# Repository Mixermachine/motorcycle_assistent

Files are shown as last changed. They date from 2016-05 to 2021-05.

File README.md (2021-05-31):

# Motorcycle Assistent

## Describtion
I created this project to equipe my BMW F650 GS motorcycle with a little assitent including a digital chain oiler.<br />

What is a chain oiler? <br />
A chain oiler drops a little amount of oil on the heavily stressed motorcycle chain.<br />
This way the chain lasts longer. <br />

Why a digital chain oiler? <br />
Regular chain oilers are often not precise, hard to adjust and finaly quite expensive.<br />
In this project I use verily cheap components with an easy-to-use interface.<br />

For controlling my Assistent I added a display, external chips and one button.<br />
The program variables, log and comments are all written in english.<br />
The user interface is designed for German users.<br />
I could provide a interface for Englisch users if there is a need for it.<br />

It runs on the Arduino/Genuino Nano and Arduino/Genuino Uno<br />

## Features:
+ Trigger the chain oiler pump after a given periode of time for a little interval
+ Display temperature
+ Display battery voltage
+ Display date and time (dim display accourding to the time)
+ Provide a menu for the settings
+ Power saving mode
+ Crank assistent (shows lowest voltage and the duration)

## Hardware:
+ Arduino nano/uno   (Uno for development, Nano for the actual use in my motorcycle)
+ SSD1306 display
+ DS18B20 temperature sensor
+ DS3231 clock chip
+ 2 * 4,7k, 2 * 12k Ohm Resistor
+ Button
+ Energy-saving voltage regulator (not compulsory, MCP1703 recomended)
+ Wiring

## Libraries
+ SPI.h (screen)
+ Wire.h (screen and clock)
+ Adafruit_GFX.h (screen)
+ Adafruit_SSD1306.h (screen)
+ OneWire.h (temperature)
+ DS3231.h (clock)
+ EEPROM.h (EEPROM memory)
+ LowPower.h (power saving)

## Chain oiler
The chain oiler can be trimmed to your needs.<br />
The pump duration time, the interval time and the state (if it works at all) can be easily set in the menu.<br />
All settings are saved in the internal memory (EEPROM) and will be loaded with each power up.<br />
The chain oiler only works if the battery voltage is above 13,2V.<br />
This is no technical limitation, but a safety one.<br />
On my F650 I needed to grab power from the rear lights, which means if I leave the parking lights on my bike on, the Arduino is still powered.<br />
If the engine is running, the generator will hold the voltage at 13,5V to 14,2V -> which means the chain oiler will run if it is set active.<br />

## Typical display faces
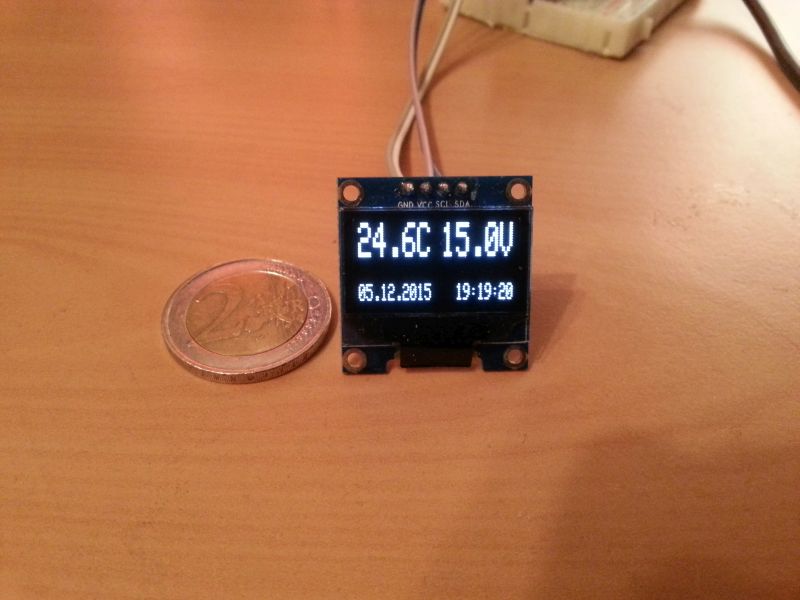
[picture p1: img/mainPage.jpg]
Main page


After a long click on the button (1 second, state 2016-05-12) the menu will open

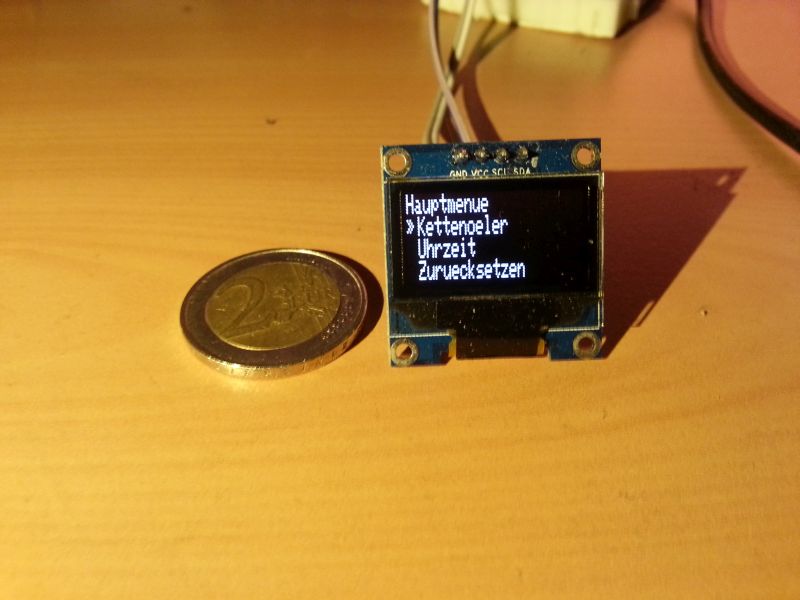
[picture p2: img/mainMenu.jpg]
Main menu


With a short click on the button you move the cursor one step further down (on the last entry it will jump back up again).<br />
With a long click on the button you enter submenus and select options.<br />
As long you are in the menu the chain oiler and all other components will remain in standby.<br />

## Voltage regulator and power saving
I recommend to replace the onboard voltage regulator with one which has less quiescent current (current which the regulator needs for itself) if you are planning to use the power saving mode. <br />
The standard one uses about 10 mA and requiers at least 7V to produce a good 5V line for the Arduino. <br />
The MCP1703 for example uses only 0.003 mA for itself and requiers 0,1V to 0,6V extra above the 5V for the Arduino to work properly. <br />
DC-DC converters do not really make sense here.<br />
Although the converter would be more efficient in the normal work mode, it would be horrible in power saving mode (because it also has a fairly high quiescent current). We don't really need a high efficiency if the engine is running (about 50mA in normal mode). <br />
To decrease the comsumption even more, you can disconnect the power LED of the Arduino.<br />

So if you use the MCP1703 and remove the power LED from the Arduino it will be much more efficient.<br />
The current should be under 0,01 mA. (Needs testing)<br />
The power saving mode will kick in if the voltage is under 12V for longer then 20 seconds.<br />
It will turn of the power of the display, clock and temperature sensor.<br />
Every 2 seconds the Arduino will wake up for under 1 millisecond to check the voltage.<br />
If the voltage is equal or above 12V the Arduino will wake up and return to the normal work mode.<br />

## Schematic

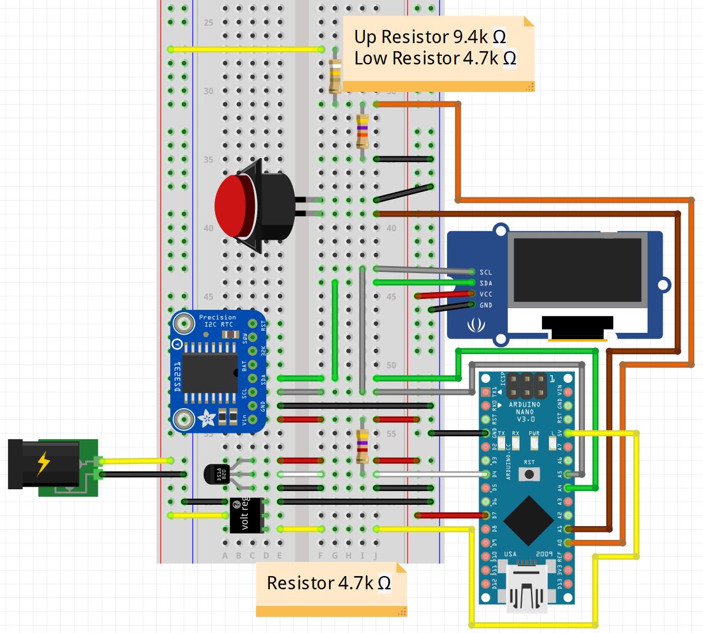
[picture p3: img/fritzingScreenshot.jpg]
Fritzing Schematic
 <br />

## Developer stuff
This project does focus on the highest efficiency possible.<br />
The Atmel328 chip (Arduino Uno, Mini,...) provides 32kb of flash memory and 2 kb of ram.<br />
I could not always focus on best practice code, but tried to keep the work well sorted and well commented.<br />
Flash memory and RAM efficiency was the main goal.<br />
The code offers the possibility of logging via the serial connection of the Arduino.<br />
Change GBL_LOGLEVEL to a value which you like. (0 verbous, 1 info, 2 warning, 3 error).<br />
This project nearly uses the hole flash memory.<br />
(state 2016-05-13, 27 148 Byte of the flash memory is used).<br />

Please open a issue here before you use this Arduino project for a commercial product.

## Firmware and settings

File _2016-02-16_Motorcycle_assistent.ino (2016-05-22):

//**** INCLUDES
//* include for Screen
#include <SPI.h>
#include <Wire.h>
#include <Adafruit_GFX.h>
#include <Adafruit_SSD1306.h>
//*

//* include for DS18B20 temperature sensor
#include <OneWire.h>
//

//* include for DS3231 clock chip
#include <DS3231.h>
//*

// include for EEPROM memory
#include <EEPROM.h>
//*

// include for the power saving sleep library
#include <LowPower.h>
//*

//**** DEFINES
//* define power pin to switch the external chips
#define POWER_PIN_EXTERNAL 7 
//*

//* define for Screen
//#define OLED_RESET 4 // not used here/ nicht genutzt bei diesem Display
Adafruit_SSD1306 display(0); // the value is not important
//#define DRAW_DELAY 118
//#define D_NUM 47
//*

//* define for DS18B20 temperature sensor
#define DS18B20_PIN 4 // PIN for temp sensor
//*

//* define for the voltageDeviderPins and resistorValue
#define VOLTAGE_PIN A0
#define VOLTAGE_RESISTOR1 9400
#define VOLTAGE_RESISTOR2 4700
#define VOLTAGE_POWERDOWN 12
//*

//* define for the buttonPins
#define BUTTON_1 A1
#define BUTTON_2 A2

#define BUTTON_TRIGGER_VALUE 600 // if analogRead returns a value above this value, the button will be triggered
//*

//* define for the CHAIN_OILER_PIN
#define CHAIN_OILER_PIN 6
// standard values for chain_oiler
#define STD_CHAIN_OILER_ACTIVE true
#define STD_CHAIN_OILER_WAIT 600000
#define STD_CHAIN_OILER_PUMP 100
#define STD_CHAIN_OILER_VOLTAGE 13.2
//*

//* define for the logs
#define GBL_LOGLEVEL 1   // set log level here
#define VERBOUS_LOG 0
#define INFO_LOG 1
#define WARNING_LOG 2
#define ERROR_LOG 3
//*

//* defines for the memory management
#define RECORD_PRESENT_ADDR 0  // 1 byte for a byte
#define RECORD_PRESENT_VALUE_0 10 // this works as a versioning control for compactibably 
#define RECORD_PRESENT_VALUE_1 10 // Later versions might changed this number

#define RECORD_CHAIN_OILER_ADDR 2     // 7 bytes to save
//*

//**** GLOBAL VARIABLES
//* power state variables
bool currentExternalPower = false;
unsigned long timeFirstLowVoltage = 0;
uint16_t timeCranking = 0;  // about 65 seconds should be enough time ;)
float lowestCrankVoltage = 0;
float measuredVoltage = 0;
uint16_t timeToWaitPowerDown = 20000; // in milliseconds

//* timing variables
// Main display refresh
unsigned long timeSinceMainDisplayRefresh = 0;  //
#define INTERVAL_MAIN_DISPLAY_REFRESH 1000 // to keep it together, define is placed here. Using define to save ram

// Main button check
// The check is triggered every 100 ms and counts up a value if the button is pressed
// At for example 10 counts a action is triggered. So you need to hold the button down for 1 
unsigned long timeSinceMainButtonCheck = 0;
#define INTERVAL_MAIN_BUTTON_CHECK 100
byte mainButtonCounter = 0;
#define MAIN_BUTTON_COUNTER_TRIGGER 10

//* DS18B20 temperatur sensor
OneWire DS18B20ds(DS18B20_PIN);
byte DS18B20addr[8];

//* DS3231 clock chip
// define the PINS for the clock.
DS3231 DS3231rtc(A4,A5); // first SDA_PIN, second SCL_PIN on DS3231

//* chain oiler timings
boolean chain_oiler_active = STD_CHAIN_OILER_ACTIVE;
unsigned long chain_oiler_wait = STD_CHAIN_OILER_WAIT;  // unsigned long else overflow. standard 10 minutes (600000 ms)
unsigned int chain_oiler_pump = STD_CHAIN_OILER_PUMP;  // how long the pump should run in one intervall
double chain_oiler_voltage = STD_CHAIN_OILER_VOLTAGE; // needs to be tested. Determines if the engine is running
unsigned long timeSinceChainOiler = 0;

//**** setup code
void setup()   {

  //* initialize Serial connection
  Serial.begin(250000);
  //*

  powerManager(true);

  timeSinceChainOiler = millis(); // skip the first run of the chain oiler.
                                  // Nobody wants to spill oil in the garage

  readSettings();  // read settings if saved previously
}

//**** loop code
void loop() {

// meassuring voltage and checking for low voltage power down or cranking

  measuredVoltage = readVoltage();
  if(measuredVoltage <= VOLTAGE_POWERDOWN) {
    // detected low voltage. Can be low battery or cranking
    unsigned long timeFirstCrank = millis();

    if (INFO_LOG >= GBL_LOGLEVEL) {
          Serial.println(F("I: Low voltage detected"));
    }
    // think of the cranking first
    // Crank assistent
    lowestCrankVoltage = measuredVoltage;
    while (measuredVoltage < VOLTAGE_POWERDOWN && (millis() - timeFirstCrank) < timeToWaitPowerDown) {
      if (measuredVoltage < lowestCrankVoltage){ // loop till voltage is higher or voltage is low for a longer time
          lowestCrankVoltage = measuredVoltage;

          // notify user of a new lowest value
          // this takes about 30 ms
          display.clearDisplay();
          display.setTextColor(WHITE);
          display.setTextSize(2);
          display.setCursor(0,0);
          display.println(F("Starten"));
          
          display.setTextSize(1);
          display.println(F("Niedrigste Spannung"));
          
          display.print(measuredVoltage,1);
          display.print('V');
          display.display();

        }
        measuredVoltage = readVoltage();
    }
    
    
    // if the low voltage is still present, go to sleep
    if ((millis() - timeFirstCrank) >= timeToWaitPowerDown) {
      if (WARNING_LOG >= GBL_LOGLEVEL) {
          Serial.println(F("I: Low voltage continues"));
          Serial.println(F("I: Entering power saving mode"));
          Serial.flush(); // wait for the serial data to be transmited before sleeping
      }
      
      // Power saving mode
      powerManager(false);

      while(readVoltage() < VOLTAGE_POWERDOWN) {

        // Power saving mode
        // wake up each two second to check the voltage.
        // sleep time could be lower but to remain a little responsive,
        // two seconds will do
        LowPower.powerDown(SLEEP_2S, ADC_OFF, BOD_OFF);
      }
      
      if (INFO_LOG >= GBL_LOGLEVEL) {
          Serial.println(F("I: Voltage is good again"));
      }
      powerManager(true);      
      
    } else {
      // if it was a simple crank, wait one second to give the user some time
      // to view the displayed value
      if (INFO_LOG >= GBL_LOGLEVEL) {
          Serial.println(F("I: Low voltage was cranking"));
          Serial.print(F("I: Crank lowest voltage="));
          Serial.println(lowestCrankVoltage,1);
          Serial.print(F("I: Crank durration="));
          Serial.println(millis() - timeFirstCrank);
          Serial.flush();  
          // we need to wait for the Serial data to be transfered
          // else the log will be distorted
      }
      
      LowPower.powerDown(SLEEP_1S,ADC_OFF,BOD_OFF);

      // display the time the cranking toke
      display.clearDisplay();
      display.setTextColor(WHITE);
      display.setTextSize(2);
      display.setCursor(0,0);
      display.println(F("Starten"));
      display.setTextSize(1);
      display.println(F("Dauer"));
      // the actual time isn't that accurate.
      // the crank duration can differ.
      // If the Arduino calcs the menu for example then the low voltage detection will be delayed
      // Still it's usefull
      display.print(millis() - timeFirstCrank -8); // it takes 8 ms from the end of the cranking loop till this is calced
      display.print(F("ms"));
      display.display();
      
      LowPower.powerDown(SLEEP_1S,ADC_OFF,BOD_OFF);
    }
  }

  // chain oiler routine
  if(timeSinceChainOiler + chain_oiler_wait <= millis()) {
    timeSinceChainOiler = millis();
    if ( chain_oiler_active) {
      if (readVoltage() >= chain_oiler_voltage) {
        triggerChainOiler(chain_oiler_pump);
      } else {
        if (INFO_LOG >= GBL_LOGLEVEL) {
          Serial.print(F("I: Chain oiler voltage ("));
          Serial.print(readVoltage());
          Serial.println(F(") to low"));
        }
      }
    } else {
      if (INFO_LOG >= GBL_LOGLEVEL) {
        Serial.println(F("I: Chain oiler timer triggered, but chain oiler is set inactive"));
      }
    }   
  }
  
  // main display update routine
  if (millis() - timeSinceMainDisplayRefresh >= INTERVAL_MAIN_DISPLAY_REFRESH) {
    timeSinceMainDisplayRefresh = millis();  // reset it here to avoid the 50 ms delay of the display
    
    display.clearDisplay();
    display.setTextColor(WHITE);
    
    // display temperatur
    display.setTextSize(2);
    display.setCursor(0,0);
    display.print(readTemperatur(),1);     // takes about 23 - 24 ms
    display.println('C');
  
    // display voltage
    display.setTextSize(2);
    String voltageTempString = String(readVoltage(),1)+"V";  //  takes about 3 - 4 ms
    // determining if the voltage value length is 4 or 5 digits long
    if (voltageTempString.length() == 4) {    
      display.setCursor(80,0);
    } else {
      display.setCursor(68,0);
    }                  
    display.println(voltageTempString);
  
    // display date
    display.setTextSize(1);
    display.setCursor(0,25);
    display.println(DS3231rtc.getDateStr());  // takes about 3 - 4 ms
  
    // display time
    display.setCursor(80,25);
    char* tempTimeString = DS3231rtc.getTimeStr();
    display.println(tempTimeString);  // takes about 3 - 4 ms
  
    if(tempTimeString[0] == 50 && tempTimeString[1] >= 48 && tempTimeString[1] <= 52) { 
      // if first digit of the current hour is 2
      // and second digit of the current hour is between 0 and 4 (keep it easy to edit)
      if (VERBOUS_LOG >= GBL_LOGLEVEL) {
        Serial.println(F("V: Display dimmed"));
      }
      display.dim(true); // dim display
  
    } else if(tempTimeString[0] == 48 && tempTimeString[1] >= 48 && tempTimeString[1] <= 56) {
       // if first digit of the current hour is 0
       // if second digit of the current hour is between 0 and 8 (keep it easy to edit)
       if(VERBOUS_LOG >= GBL_LOGLEVEL) {
        Serial.println(F("V: Display dimmed"));
       }
       display.dim(true); // dim display
    } else {
      if(VERBOUS_LOG >= GBL_LOGLEVEL) {
        Serial.println(F("V: Display not dimmed"));
      }
      display.dim(false);    
    }
    
    display.display();
  }
  
  // button check routine
  // counts up if button is presse
  // switches to menu if counts hit a certain level
  
  if (millis() - timeSinceMainButtonCheck >= INTERVAL_MAIN_BUTTON_CHECK) {
    timeSinceMainButtonCheck = millis();
    
    // the button needs to pressed for a certain time before a action is triggerd (to prevent false input)
    // this can't be done by any other method. The display should get updated even if the button is pressed
    if(analogRead(BUTTON_1) > BUTTON_TRIGGER_VALUE) {
      mainButtonCounter++;
  
      // if trigger is reached enter menu
      if(mainButtonCounter >= MAIN_BUTTON_COUNTER_TRIGGER) {
        if(INFO_LOG >= GBL_LOGLEVEL) {
          Serial.println(F("I: Entering Menu"));
        }
        enterMenuPage();
        mainButtonCounter= 0;  // resseting the counter
      }
      
    } else {
      mainButtonCounter = 0;
    }
  }

}

// MENU TASK
// this displays the menu for the user
// Nothing else will and should happen if the user is in the menu.
// Everything is packed into one methode to save space in RAM and Flash
// It takes quite a amount of extra stuff to draw and control the menu
// So, not that pretty stuff here, but it's functional
void enterMenuPage() {
  boolean exitMenu = false;

  // is needed to wait for the user
  boolean firstPageDisplay = false;
  
  // Menu defines.
  // Not at the top, because a user does not really needs to change this values
  // menuTyps
  // 0 first page
  #define MENU_FIRST_PAGE_ITEMS_COUNT 4
  // 10 chain oiler
  #define MENU_CHAIN_OILER_ITEMS_COUNT 6
  // 20 clock 
  #define MENU_CLOCK_ITEMS_COUNT 13
  // 90 reset all settings
  #define MENU_RESET_SETTINGS_ITEMS_COUNT 2

  byte menuTyp = 0;

  #define MENU_POINTER_GAB 8
  #define MENU_ENTRY_HEIGHT 8
  #define MENU_FIRST_ENTRY 8
  #define MENU_OFFSET_MOVE_TRIGGER 2  // defines when the menu should start to shift the text upwards

  byte menu_item_count = 3;
  byte menu_Pointer_Location = 0;
  byte menuOffset = 0;  // moves the hole menu up to display new stuff. Dealing with the small display

  // is true if the last press was registered as a long press
  // will be set to false after the next check
  boolean lastPressLong = false;


  // Print a reminder message, to not use the menu while driving
  display.clearDisplay();
  display.dim(false);

  display.setCursor(0,0);
  display.setTextSize(1);
  display.println(F("BEDIENUNG WAEHREND\nDER FAHRT VERBOTEN"));
  display.setCursor(0,17);
  display.println(F("Oeler im Menue \n deaktiviert"));

  display.display();

  getButtonHoldTime(BUTTON_1, false);  // simply wait for the user to release the button

  // printig the menu in a loop and handling the button
  while(!exitMenu){

  // printing section

  display.clearDisplay();
  
    switch(menuTyp) {
      case 0:   // main menu
      // found a bug in the compiler code maybe?
      // without the extra {} which creates an extra scope the sketch won't compile
      // i do not double use variables in different cases
      // the error appears when somewhere in a case a string is initialized (not matter what name it has)
      // the error always appears afte case 20
      { 
        menu_item_count = MENU_FIRST_PAGE_ITEMS_COUNT;  // dealing with the menu hops
        // Headline
        display.setCursor(0,0 - menuOffset);
        display.setTextSize(1);
        display.println(F("Hauptmenue"));
      
        // Menu points
        display.setTextSize(1);
        display.setCursor(MENU_POINTER_GAB,MENU_FIRST_ENTRY + MENU_ENTRY_HEIGHT * 0 - menuOffset);
        display.print(F("Kettenoeler"));
      
        display.setCursor(MENU_POINTER_GAB,MENU_FIRST_ENTRY + MENU_ENTRY_HEIGHT * 1 - menuOffset);
        display.print(F("Uhrzeit"));
      
        display.setCursor(MENU_POINTER_GAB,MENU_FIRST_ENTRY + MENU_ENTRY_HEIGHT * 2 - menuOffset);
        display.print(F("Zuruecksetzen"));
    
        display.setCursor(MENU_POINTER_GAB,MENU_FIRST_ENTRY + MENU_ENTRY_HEIGHT * 3 - menuOffset);
        display.print(F("Zurueck"));
      }
      break;

      case 10:  // chain oiler menu
      {
        menu_item_count = MENU_CHAIN_OILER_ITEMS_COUNT;
  
        // Headline
        display.setCursor(0,0 - menuOffset);
        display.setTextSize(1);
        display.print(F("Kettenoeler"));
  
        // display wait and pump time on the right side
        display.setCursor(96,0);  // no menuOffset here. We need to see what we change
        display.print(chain_oiler_wait/1000);
        display.print('s');
  
        display.setCursor(96,8);
        display.print(chain_oiler_pump);
        display.print(F("ms"));
    
         // Menu points
        display.setTextSize(1);
        display.setCursor(MENU_POINTER_GAB,MENU_FIRST_ENTRY + MENU_ENTRY_HEIGHT * 0 - menuOffset);
        display.print(F("Status:"));
        if(chain_oiler_active) {
          display.print(F("aktiv"));
        } else {
          display.print(F("inaktiv"));
        }
        
        display.setCursor(MENU_POINTER_GAB,MENU_FIRST_ENTRY + MENU_ENTRY_HEIGHT * 1 - menuOffset);
        display.print(F("Wartezeit +30s"));
      
        display.setCursor(MENU_POINTER_GAB,MENU_FIRST_ENTRY + MENU_ENTRY_HEIGHT * 2 - menuOffset);
        display.print(F("Wartezeit -30s"));
  
        display.setCursor(MENU_POINTER_GAB,MENU_FIRST_ENTRY + MENU_ENTRY_HEIGHT * 3 - menuOffset);
        display.print(F("Interval +10ms"));
  
        display.setCursor(MENU_POINTER_GAB,MENU_FIRST_ENTRY + MENU_ENTRY_HEIGHT * 4 - menuOffset);
        display.print(F("Interval -10ms"));
      
        display.setCursor(MENU_POINTER_GAB,MENU_FIRST_ENTRY + MENU_ENTRY_HEIGHT * 5 - menuOffset);
        display.print(F("Zurueck"));
      }
      break;

      case 20:  // clock menu 
      {
        menu_item_count = MENU_CLOCK_ITEMS_COUNT;
        
        // Headline
        display.setCursor(0,0 - menuOffset);
        display.print(F("Uhrzeit"));

        if(menu_Pointer_Location < 6) {
          // display time on the right side. Horizontal
          char* tempSettingsTime = DS3231rtc.getTimeStr();
          display.setCursor(100,8);
          display.print(tempSettingsTime[0]);
          display.print(tempSettingsTime[1]);
          display.print('H');
          display.setCursor(100,16);
          display.print(tempSettingsTime[3]);
          display.print(tempSettingsTime[4]);
          display.print('M');
          display.setCursor(100,24);
          display.print(tempSettingsTime[6]);
          display.print(tempSettingsTime[7]);
          display.print('S');
        } else {
          char* tempSettingsDate = DS3231rtc.getDateStr();
          
          display.setCursor(100,8);
          display.print(tempSettingsDate[0]);
          display.print(tempSettingsDate[1]);
          display.print('D');
          display.setCursor(100,16);
          display.print(tempSettingsDate[3]);
          display.print(tempSettingsDate[4]);
          display.print('M');
          display.setCursor(90,24);
          display.print(tempSettingsDate[6]);
          display.print(tempSettingsDate[7]);
          display.print(tempSettingsDate[8]);
          display.print(tempSettingsDate[9]);
          display.print('Y');
        }
        

        display.setCursor(MENU_POINTER_GAB,MENU_FIRST_ENTRY + MENU_ENTRY_HEIGHT * 0 - menuOffset);
        display.print(F("+5 sek"));

        display.setCursor(MENU_POINTER_GAB,MENU_FIRST_ENTRY + MENU_ENTRY_HEIGHT * 1 - menuOffset);
        display.print(F("-5 sek"));
      
        display.setCursor(MENU_POINTER_GAB,MENU_FIRST_ENTRY + MENU_ENTRY_HEIGHT * 2 - menuOffset);
        display.print(F("+1 min"));
  
        display.setCursor(MENU_POINTER_GAB,MENU_FIRST_ENTRY + MENU_ENTRY_HEIGHT * 3 - menuOffset);
        display.print(F("-1 min"));
  
        display.setCursor(MENU_POINTER_GAB,MENU_FIRST_ENTRY + MENU_ENTRY_HEIGHT * 4 - menuOffset);
        display.print(F("+1 std"));
      
        display.setCursor(MENU_POINTER_GAB,MENU_FIRST_ENTRY + MENU_ENTRY_HEIGHT * 5 - menuOffset);
        display.print(F("-1 std"));
        
        display.setCursor(MENU_POINTER_GAB,MENU_FIRST_ENTRY + MENU_ENTRY_HEIGHT * 6 - menuOffset);
        display.print(F("+1 tag"));
        
        display.setCursor(MENU_POINTER_GAB,MENU_FIRST_ENTRY + MENU_ENTRY_HEIGHT * 7 - menuOffset);
        display.print(F("-1 tag"));
        
        display.setCursor(MENU_POINTER_GAB,MENU_FIRST_ENTRY + MENU_ENTRY_HEIGHT * 8 - menuOffset);
        display.print(F("+1 mon"));
        
        display.setCursor(MENU_POINTER_GAB,MENU_FIRST_ENTRY + MENU_ENTRY_HEIGHT * 9 - menuOffset);
        display.print(F("-1 mon"));
        
        display.setCursor(MENU_POINTER_GAB,MENU_FIRST_ENTRY + MENU_ENTRY_HEIGHT * 10 - menuOffset);
        display.print(F("+1 jahr"));
        
        display.setCursor(MENU_POINTER_GAB,MENU_FIRST_ENTRY + MENU_ENTRY_HEIGHT * 11 - menuOffset);
        display.print(F("-1 jahr"));
        
        display.setCursor(MENU_POINTER_GAB,MENU_FIRST_ENTRY + MENU_ENTRY_HEIGHT * 12 - menuOffset);
        display.print(F("Zurueck"));
        
      }
      break;

      case 90: // reset settings menu
      {
        menu_item_count = MENU_RESET_SETTINGS_ITEMS_COUNT;

        // Headline
        display.setCursor(0,0 - menuOffset);
        display.print(F("Zuruecksetzen"));
    
        // to be sure the user really wants to reset all data
        display.setCursor(MENU_POINTER_GAB,MENU_FIRST_ENTRY + MENU_ENTRY_HEIGHT * 0 - menuOffset);
        display.print(F("Sicher zuruecksetzen"));
    
        display.setCursor(MENU_POINTER_GAB,MENU_FIRST_ENTRY + MENU_ENTRY_HEIGHT * 1 - menuOffset);
        display.print(F("Zurueck"));
      }
      break;
    }

    // print the menu pointer
    display.setCursor(0, MENU_FIRST_ENTRY + menu_Pointer_Location * MENU_ENTRY_HEIGHT - menuOffset);
    display.print((char)175);
    

    display.display();

  // action section
  // get the input from the user
  // if this is the first display of a new menuPage then wait for the user to release the button
    unsigned int button_1_hold = 0;
    if (firstPageDisplay) {
      getButtonHoldTime(BUTTON_1, false);
      firstPageDisplay = false;
    } else {
      button_1_hold = getButtonHoldTime(BUTTON_1, true);
    }
    
    // first find out if the button was a long press
    // reusing the predefined value for the button long press trigger (100ms * 10ms) = 1000 ms
    if(button_1_hold >= INTERVAL_MAIN_BUTTON_CHECK * MAIN_BUTTON_COUNTER_TRIGGER) {
      switch(menuTyp) {
        case 0:   // main menu
        switch(menu_Pointer_Location) {
          case 0:  // enter chain oiler menu
          menuTyp = 10;
          menu_Pointer_Location = 0;
          firstPageDisplay = true;
          break;
          case 1:  // enter clock menu
          menuTyp = 20;
          menu_Pointer_Location = 0;
          firstPageDisplay = true;
          break;
          case 2:  // reset settings
          menuTyp = 90;
          menu_Pointer_Location = 0;
          firstPageDisplay = true;
          break;
          case 3:
          exitMenu = true;
          break;
          
        }        
        break;
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

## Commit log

2016-03-27 Arduino build
2016-04-03 Working on the menu
    Pieces of the menu are no longer divided into many methods.
    Only one for now. (To save RAM and FLASH memory)
    [_2016-02-16_Motorcycle_assistent.ino]
2016-04-03 Working on the menu
    Finished the main menu page and the chain oiler menu
2016-04-03 Working on the menu
    Started working on clock menu
    Build is functional, but the clock menu is not working
    [_2016-02-16_Motorcycle_assistent.ino]
2016-04-03 Working on the menu
    Delayed safe of the Arduino IDE...
2016-04-11 Saving function has arrived
    Chain oiler settings are saved
2016-05-08 The menu is now fully functional Added: Clock menuPage Modified: Preparation for powerDown mod (mapping power to pin4) Modified: Some misc changes
2016-05-12 Readability and new feature for README.md
    Inserting <br /> to make the text more readable and adding the feature entry "crank assistent"
2016-05-13 new: power saving, powerManager and crank assistent
    Introducing:
    - Power saving power mode
    - powerManager(boolean) (power on/off external chips)
    - Crank assistent
    chain oiler has not changed
2016-05-22 Reset menu fix, Short button press fix
    Reset menu fix:
    -String was to long for the display
    Shortend it
    -Go back to higher menu layer after reset
    Short button press fix:
    -Disable shurt button press check for one menu render to prevent "extra"
    hoping after button long press
    See line 733 for a little description
    [_2016-02-16_Motorcycle_assistent.ino]
2016-05-24 Adding some things in README.rm
    -Better explanation of the project
    -Better explanation of the chain oiler
    -Misc changes
    -Spell correction
2017-03-21 Adding a schematic of the setup. Made with Fritzing
    [Fritzing_plan.fzz]
2017-03-21 Fixed naming of new files
    [fritzingSchematic.fzz]
2017-03-21 Update README.md
    Added picture of the Fritzing Schematic
    Fixed small text parts
2017-07-15 Fixed: Small error in fritzingSchematic
    [fritzingSchematic.fzz]
2017-07-15 Fixed: Bus cable are not connected correctly
    [fritzingSchematic.fzz]
